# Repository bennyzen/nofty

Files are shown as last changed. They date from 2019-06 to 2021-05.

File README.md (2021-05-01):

# Nofty
A 3D printable, vertical NFT system. This is a re-circulating NFT (Nutrient Film Technique) system without any soil or buffering medium. Consumption of water and production of waste are kept to a minimum.

This whole set of parts comes pre-rendered as STL files. You can use these files in folder `stl` to feed your slicer and print them right away. If you feel the need to customize things, refer to `config.js` as good starting point.

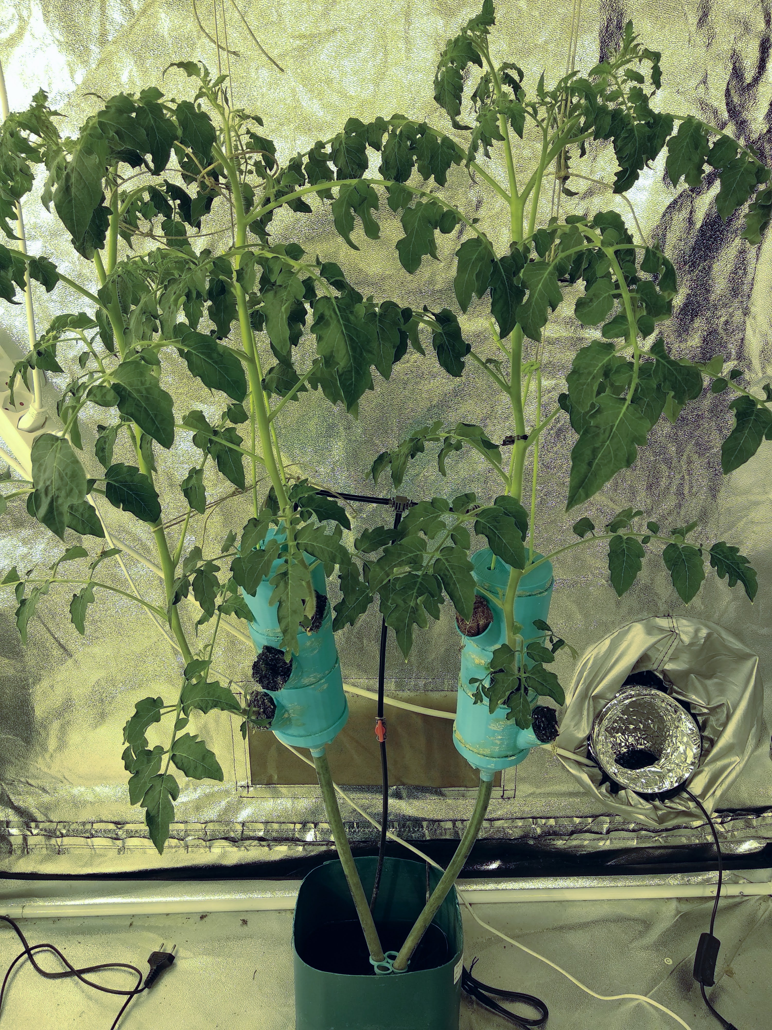
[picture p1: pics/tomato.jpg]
nofty growing tomatoes


## Things you need:
- 3D printer
- 500g PLA or PETG filament
- 1x water pump, >5W
- 1x small tank, >3L
- 1x thin rope, <2m
- 12mm tube, <2m
- fleece pad, 20x20cm

## Things to know:
- the pump should run constantly or at least in short intervals
- make sure to adjust EC and pH values of your solution according to what you grow. to know the right values for your nutrient solution refer to [this table](http://www.homehydrosystems.com/ph_tds_ppm/ph_vegetables_page.html).
- as a general rule, plants will have a higher nutrient requirement during cooler months, and a lower requirement in the hottest months. Therefore, a stronger nutrient solution should be maintained during winter, with a weaker solution during summer when plants take up and transpire more water than nutrients.

## How to print:
All my prints were done on a cheap FDM printer using PLA and a 1.0mm nozzle. The large nozzle makes prints really fast and sturdy. According to the 1.0mm nozzle, the `WALL_THICKNESS` variable in `config.js` was set to 2mm. Make sure you set your `WALL_THICKNESS` to a multiple of your nozzle width. Use at least 1.5mm or 2-5 times the nozzle width, depending on your nozzle. If you use a traditional 0.4mm nozzle, use at least a `WALL_THICKNESS` of 1.6mm to get enough stability. All pieces should be waterproof and fit into each other. The fit is crucial, so I recommend you follow the build instructions provided below to the point.

## How to build:
- print the bottom first, as it's the hardest piece. print everything from the bottom upwards.
- now print one middle segment first and make sure that it fits into the bottom piece. if it does not fit, edit the `config.js` file and play with the value `RING_INSET` until you get a snug fit.
- now go on and print the rest of the middle segments, up to 8 pieces or until you reach the max height possible with your actual pump. usually a stronger pump gives you more height and more flow, consuming more energy. 
- print the top piece. again, play with the `TOP_DIAMETER` value until it fits.
- starting from the bottom, pull the rope through both holes on equal length.
- now stack up all your middle pieces, always pulling the rope through.
- pull both ends of the rope through the holes on the inside of the top piece and make a knot.

## Printer Settings
- use `Layer Time` when layers get to short, to allow the pieces to cool down
  and prevent deformation. if your prints are deformed, the chance is high that
  the pieces won't fit into each other.
- get your extrusion right. use things like [Fast edge over/under extrusion test](https://www.thingiverse.com/thing:1622868)
  on Thingiverse to adjust your extrusion and keep it consistent across all
  your prints.

## Possible Features
- Using pH and EC circuits from [Atlas Scientific](https://www.atlas-scientific.com/product_pages/circuits/ezo_ph.html) a constant measurement could occur
- using an ESP32 the system could show pH and EC, be reachable through a web-interface 
  and report its values to the cloud

## How to operate
Once all parts are printed and fit into each other, you're ready to test your system. First of all you need to be sure there are no leaks. Even a small leak can result in a complete outage, when run for a couple of hours.

### Note
This uses JSCAD v1 which is now deprecated. Upgrading to JSCAD v2 would mean to rewrite all models. I'm not gonna do that right now, as I don't see any resulting advantage.

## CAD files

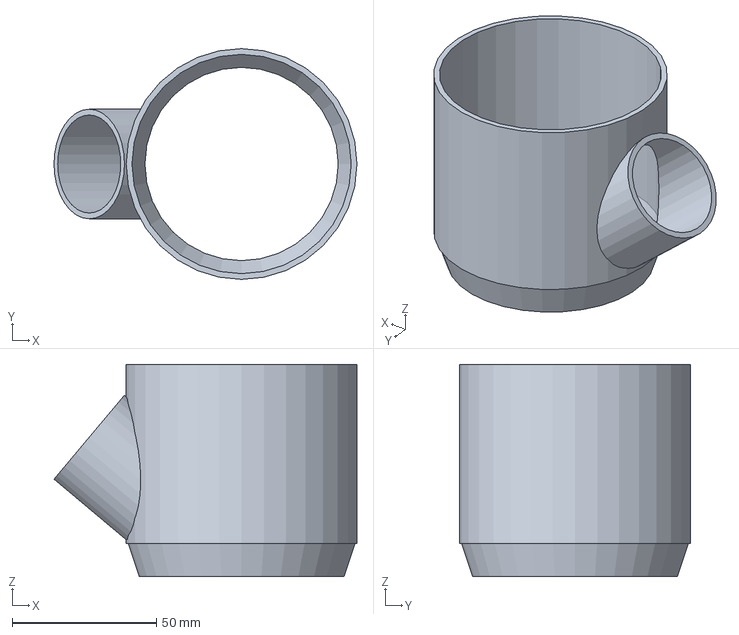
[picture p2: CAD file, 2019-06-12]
middle/middle.3mf
105.0 x 80.0 x 73.5 mm

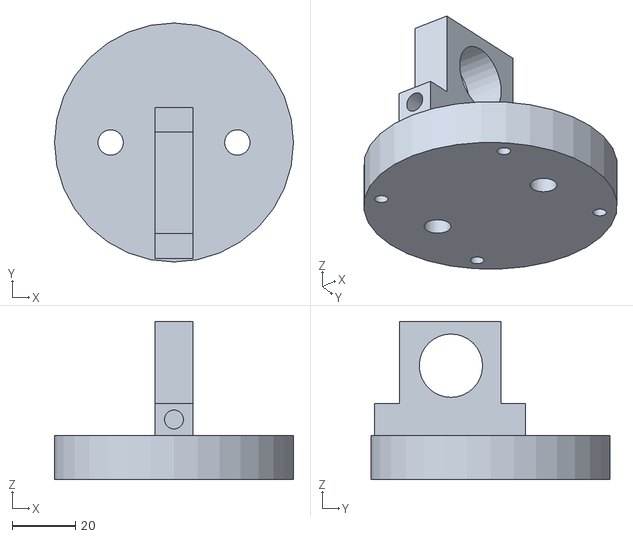
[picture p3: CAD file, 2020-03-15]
stl/top-v4.stl
75.5 x 75.5 x 50.0

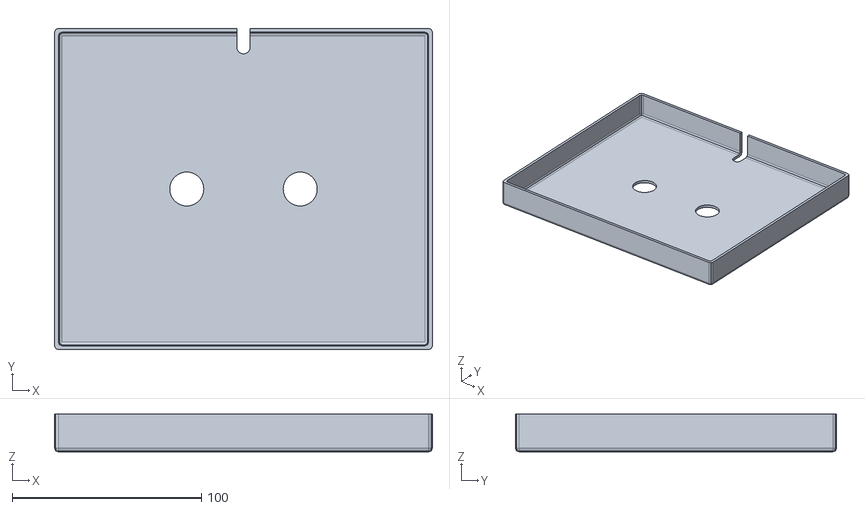
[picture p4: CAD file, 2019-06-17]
stl/nft-base-cover-v1.stl
200.0 x 170.0 x 20.0

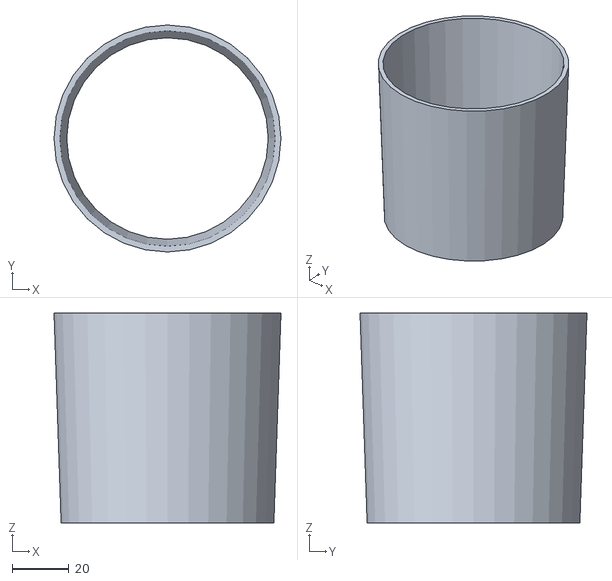
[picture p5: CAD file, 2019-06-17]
stl/middle-blind.stl
80.0 x 80.0 x 74.0

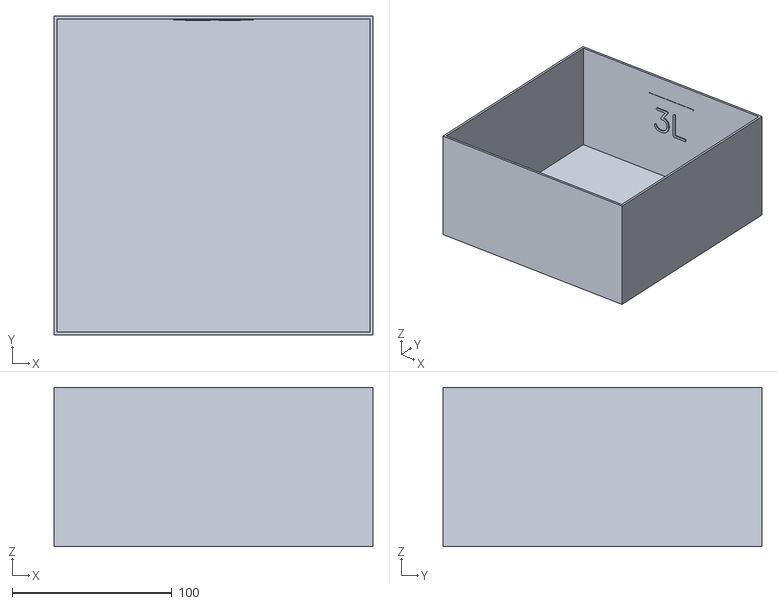
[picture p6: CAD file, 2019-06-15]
stl/base-3L.stl
200.0 x 200.0 x 100.0

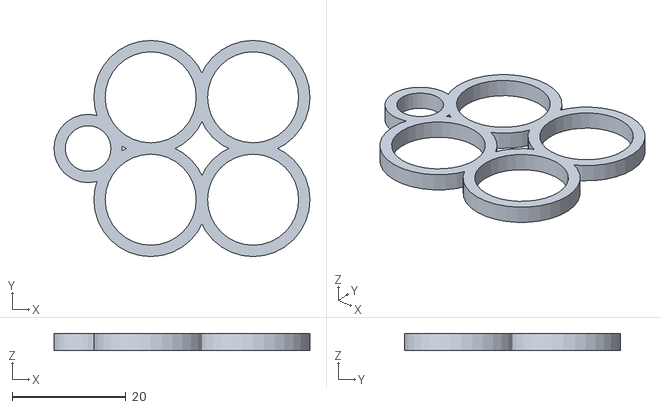
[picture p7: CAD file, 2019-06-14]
stl/tube-clip-x4.stl
45.0 x 38.0 x 3.00

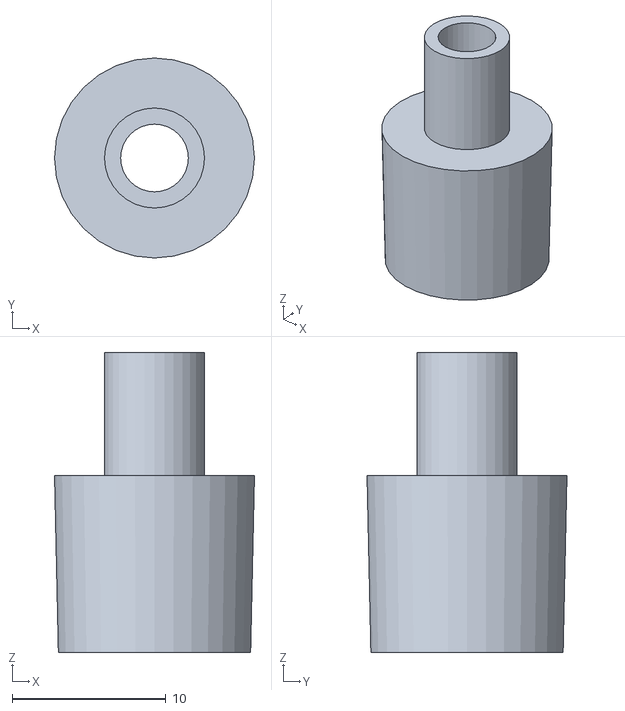
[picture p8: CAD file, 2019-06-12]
stl/pump-plug-13mm.stl
13.0 x 13.0 x 19.5

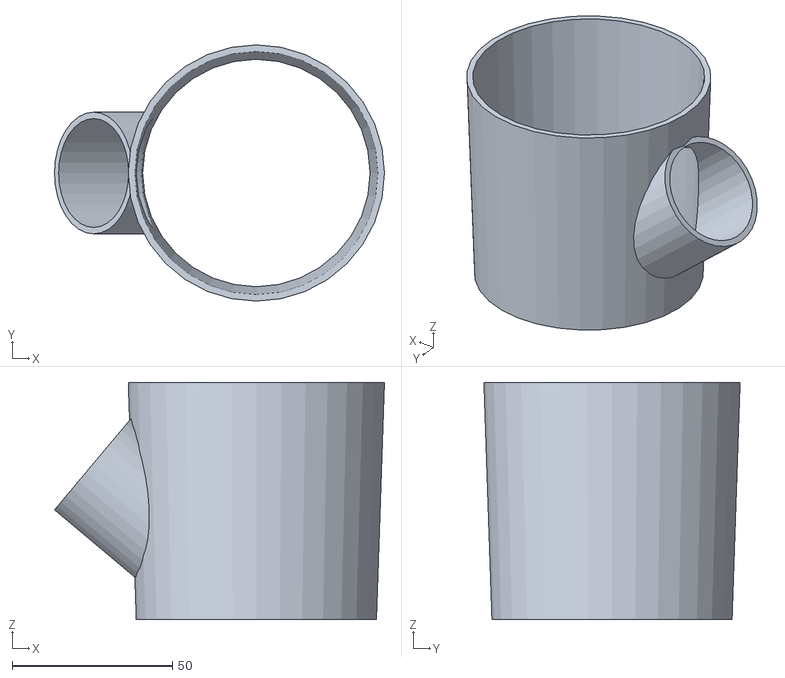
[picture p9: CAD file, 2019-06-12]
stl/middle-v2.stl
103.0 x 80.0 x 74.0

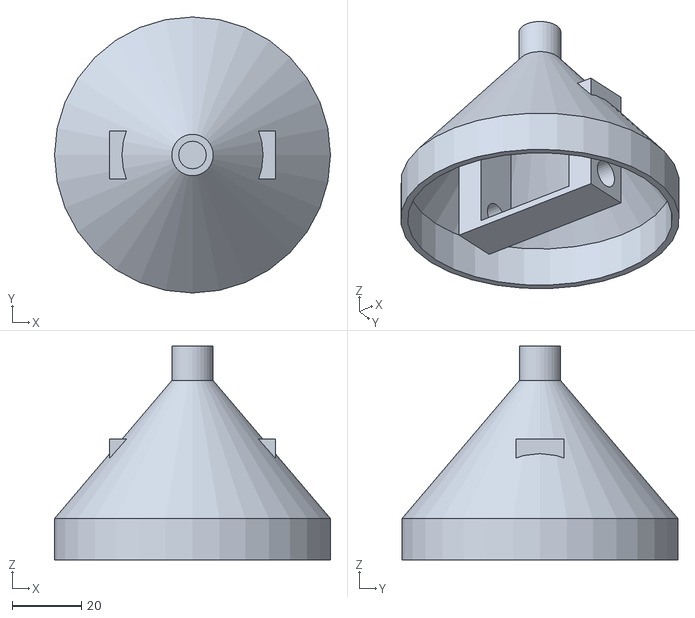
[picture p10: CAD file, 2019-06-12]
stl/bottom-v3.stl
80.0 x 80.0 x 62.0

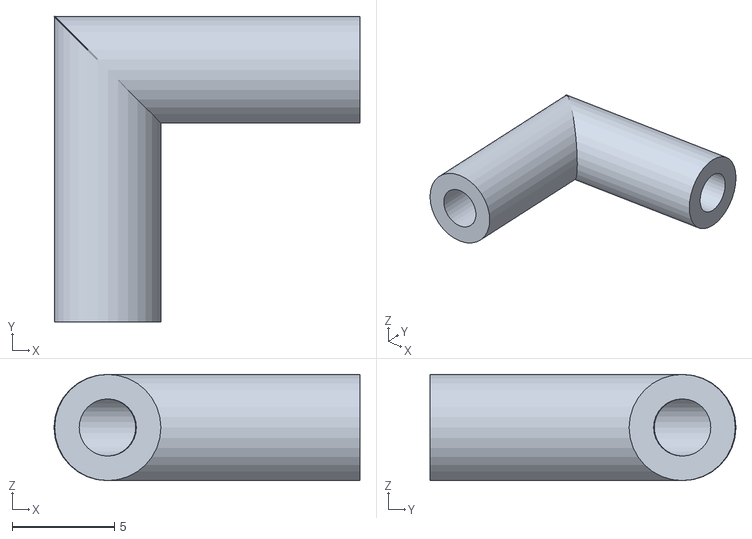
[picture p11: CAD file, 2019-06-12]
stl/4.6mm-collector-L.stl
15.0 x 15.0 x 5.20

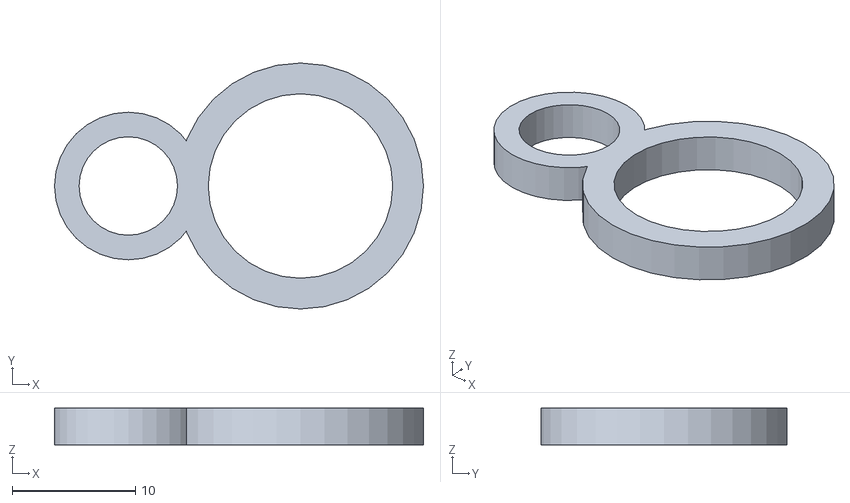
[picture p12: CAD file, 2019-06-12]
stl/tube-clip.stl
30.0 x 20.0 x 3.00

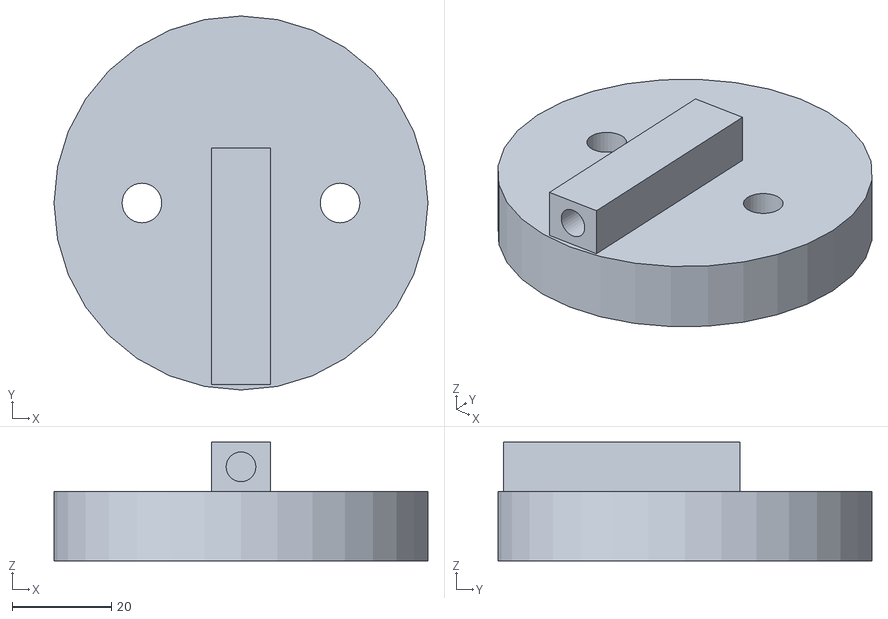
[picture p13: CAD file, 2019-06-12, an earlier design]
stl/top-v3.stl
75.5 x 75.5 x 24.0

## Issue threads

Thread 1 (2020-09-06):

outflow is too narrow

bennyzen, 2020-09-06:
The outflow on the lower part of the system is too narrow. The tubes get clogged by roots once the plants (like tomatoes) are half developed and have built a lot of root material. Once the tube is clogged, water will not recirculate back to the tank and the system will completely fail.

As only solution, I see the use of larger tubes for the back-flow.

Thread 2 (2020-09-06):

pots or baskets needed

bennyzen, 2020-09-06:
Problem: plants fall through holes.

Solution: some kind of pots or baskets that fit into the hole.

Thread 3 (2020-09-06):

inclination

bennyzen, 2020-09-06:
Problem: appending the system results in inclination, making the nutrient solution only flow on one side of the system. Plants on the other side will dry out or suffer from malnutrition over time.

Solution: some kind of frame that will prevent inclination.

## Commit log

2019-06-08 working example
    [test.stl]
2019-06-12 removes the test
    [test.stl]
2019-06-12 adding STLs
    [4.6mm-collector-L.stl, bottom-v1.stl, bottom-v2.stl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]
2019-06-12 adds all previous versions
    [middle.3mf]
2019-06-12 removes this faulty segment
    [segment.stl]
2019-06-12 removing obsoleted STLs, preventing them from accidentally being printed
    [bottom-v1.stl, bottom-v2.stl, top-v1.stl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]
2019-06-14 adds a clip tu fix 4 big and one small tubes together
    [tube-clip-x4.stl]
2019-06-15 adds an incomplete base
    [base-3L.stl]
2019-06-17 adds some NFT stuff that does not belong here
    [nft-baseplate-hooks.stl, nft-clip.stl, nft-tissue-pad1.stl]
2019-06-17 adds a middle blind piece
    [middle-blind.stl]
2019-06-17 adds a clip for the upper nft cover
    [nft-stick-clip-3mm.stl]
2019-06-17 adds a cover for the base tank
    [nft-base-cover-v1.stl]
2019-06-19 adds a new version that should hopefully work better and distribute the nutrient more even across the walls
    [top-v4.stl]
2020-03-15 removing files that do not belong here from project
    [nft-baseplate-hooks.stl, nft-clip.stl, nft-stick-clip-3mm.stl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]
2020-03-15 adds rendered stl of top v4
    [top-v4.stl]
